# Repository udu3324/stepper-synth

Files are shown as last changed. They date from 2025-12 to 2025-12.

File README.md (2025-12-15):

# stepper-synth

An electronic instrument that uses stepper motors to make music. Powered by the esp32 ecosystem, it is a synthesizer with 3 octaves with velocity support using hall effect sensors. It is inspired by the musician/engineer [Love Hultén](https://www.youtube.com/@hulten1000).

## Why I Made This

There's so many electronic instruments that make sounds purely through cables and rely on other devices to output to them. Instead, what if I used the power of stepper motors to make sound and create a standalone device? I notice how harmonic these motors could be while 3d printing, they sometimes have a noticable pattern and variable pitch that can be utilized.

## Photos

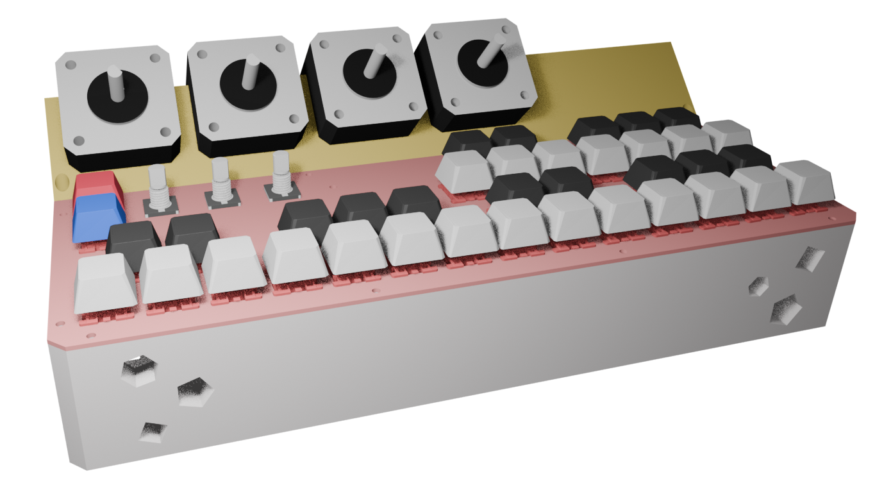
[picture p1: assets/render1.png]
render

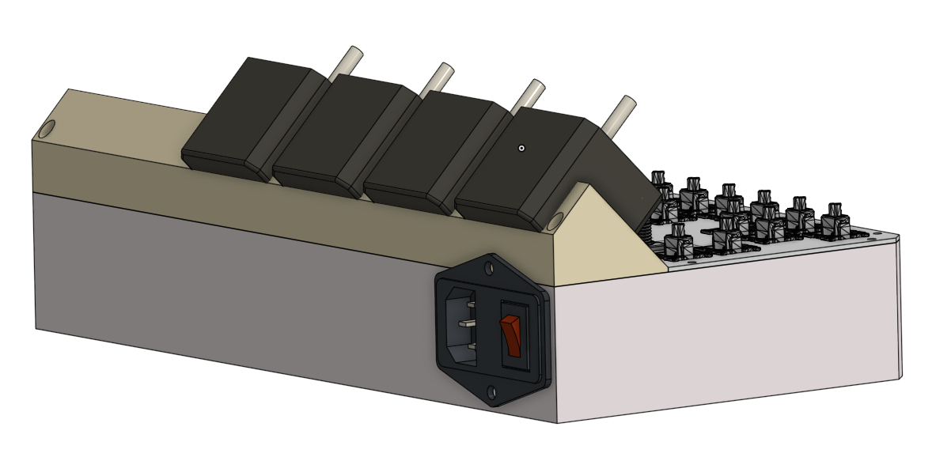
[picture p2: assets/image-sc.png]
sc1

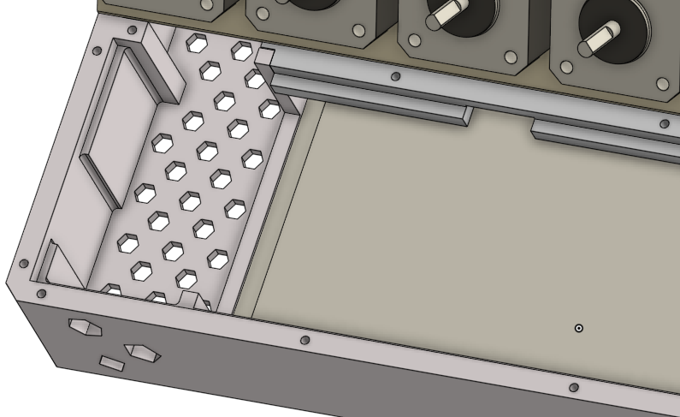
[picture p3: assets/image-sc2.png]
sc2


## PCB

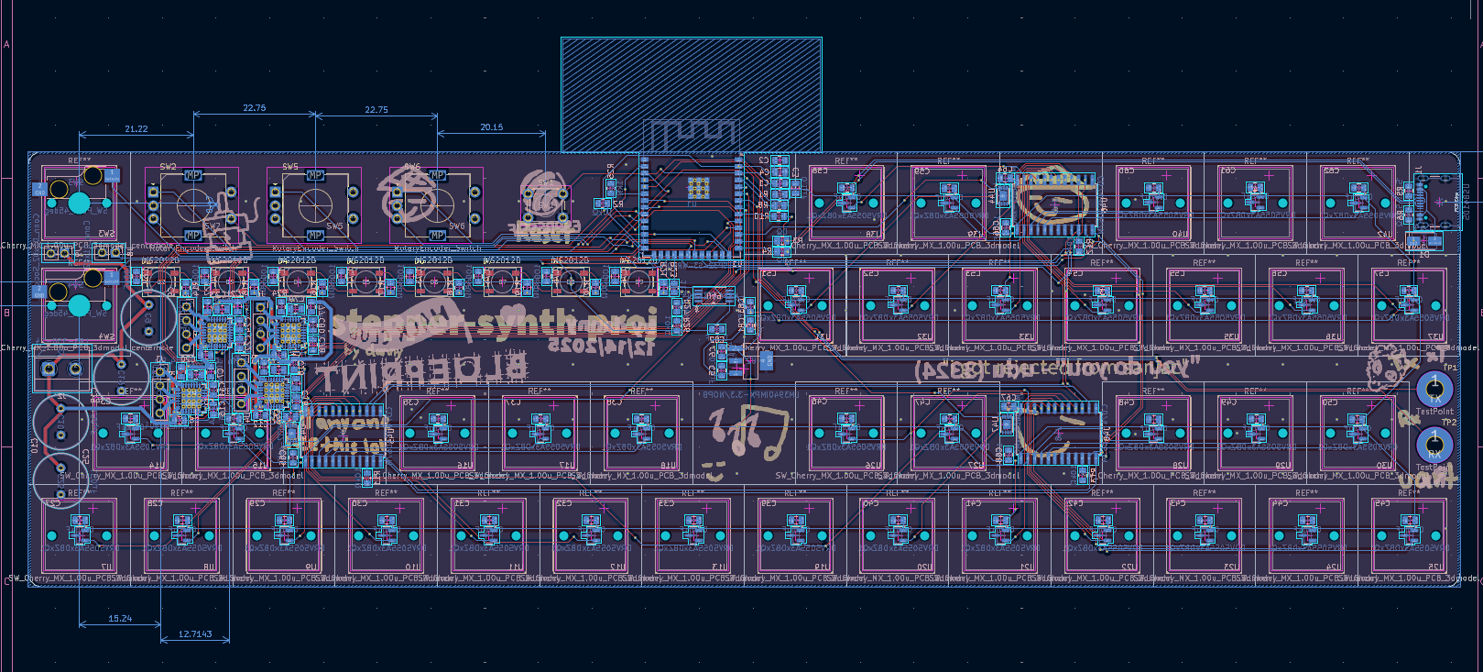
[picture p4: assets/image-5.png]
pcb

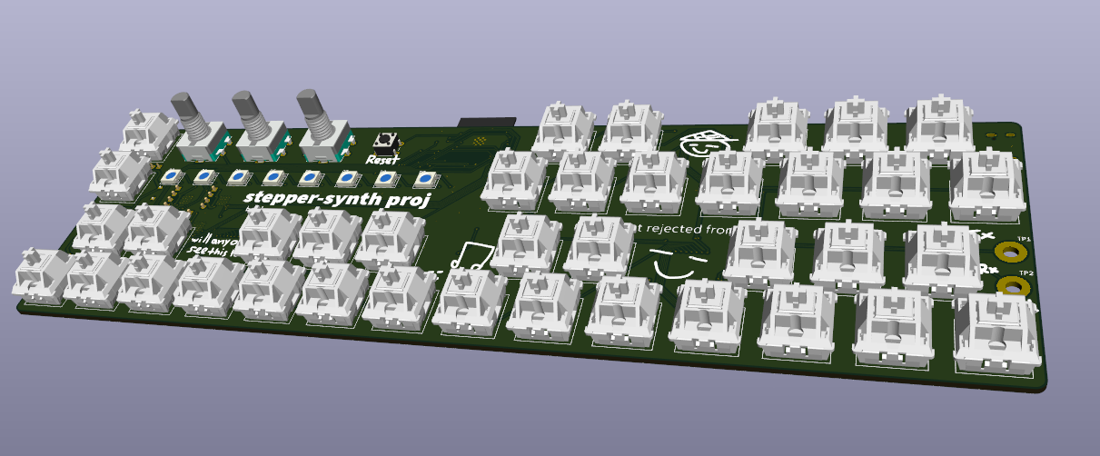
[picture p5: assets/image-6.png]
3d pcb


## Schematics

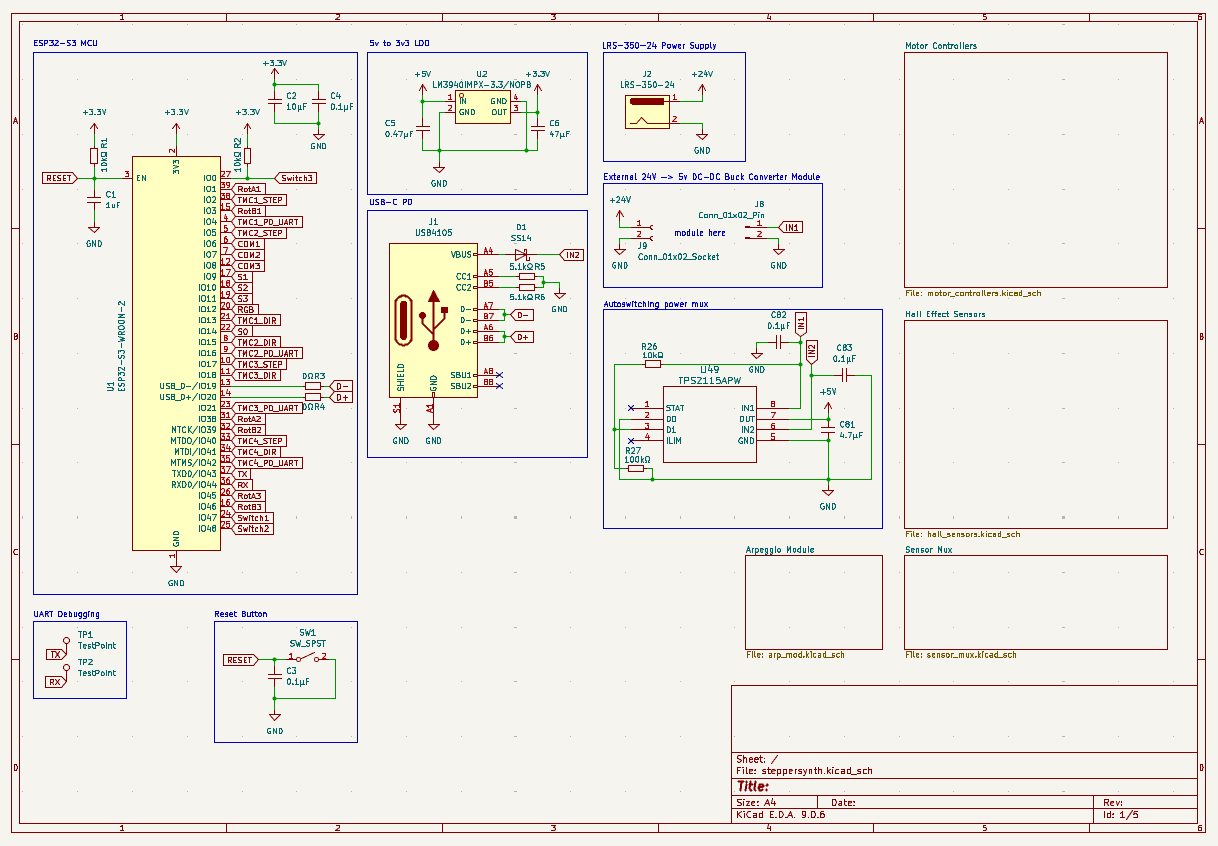
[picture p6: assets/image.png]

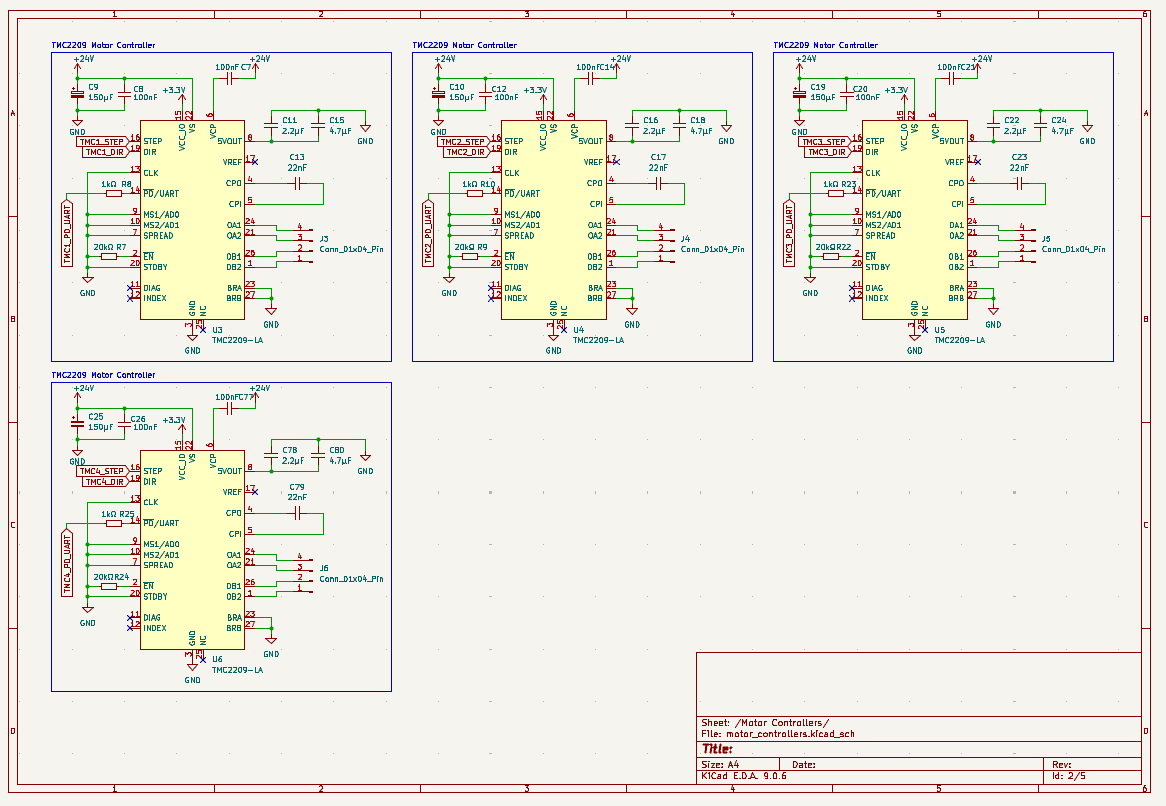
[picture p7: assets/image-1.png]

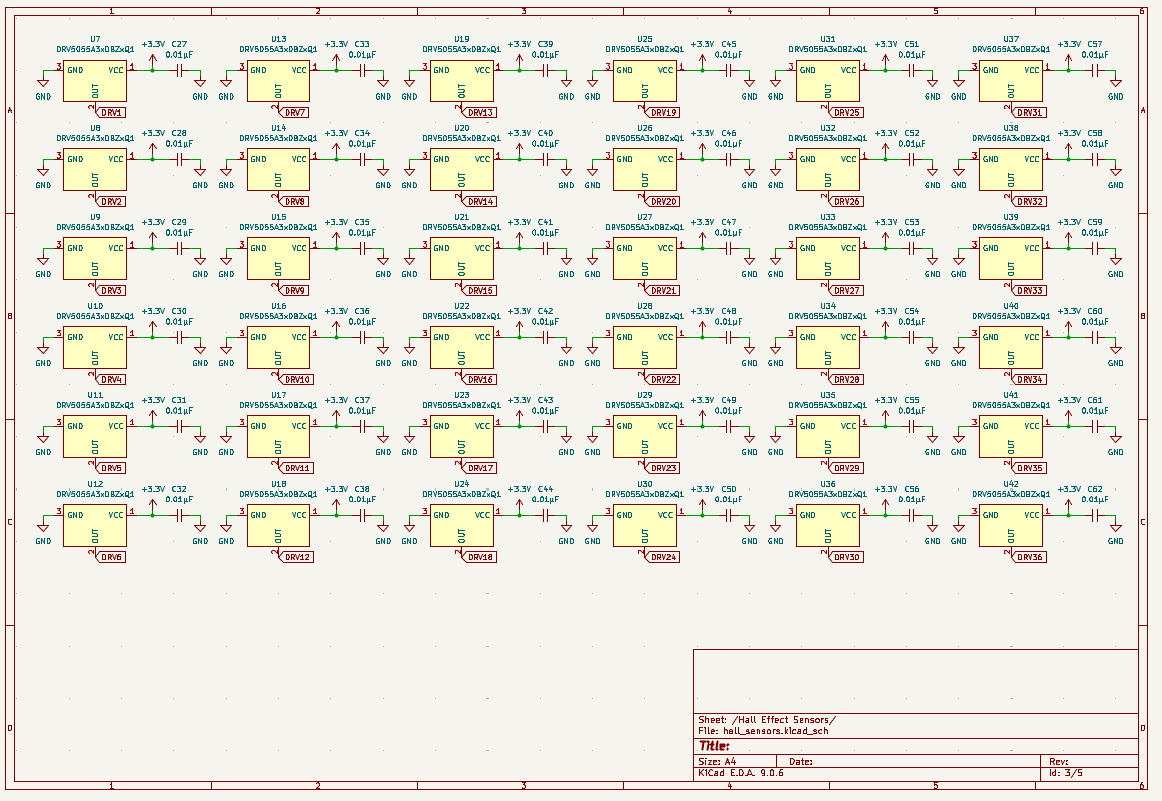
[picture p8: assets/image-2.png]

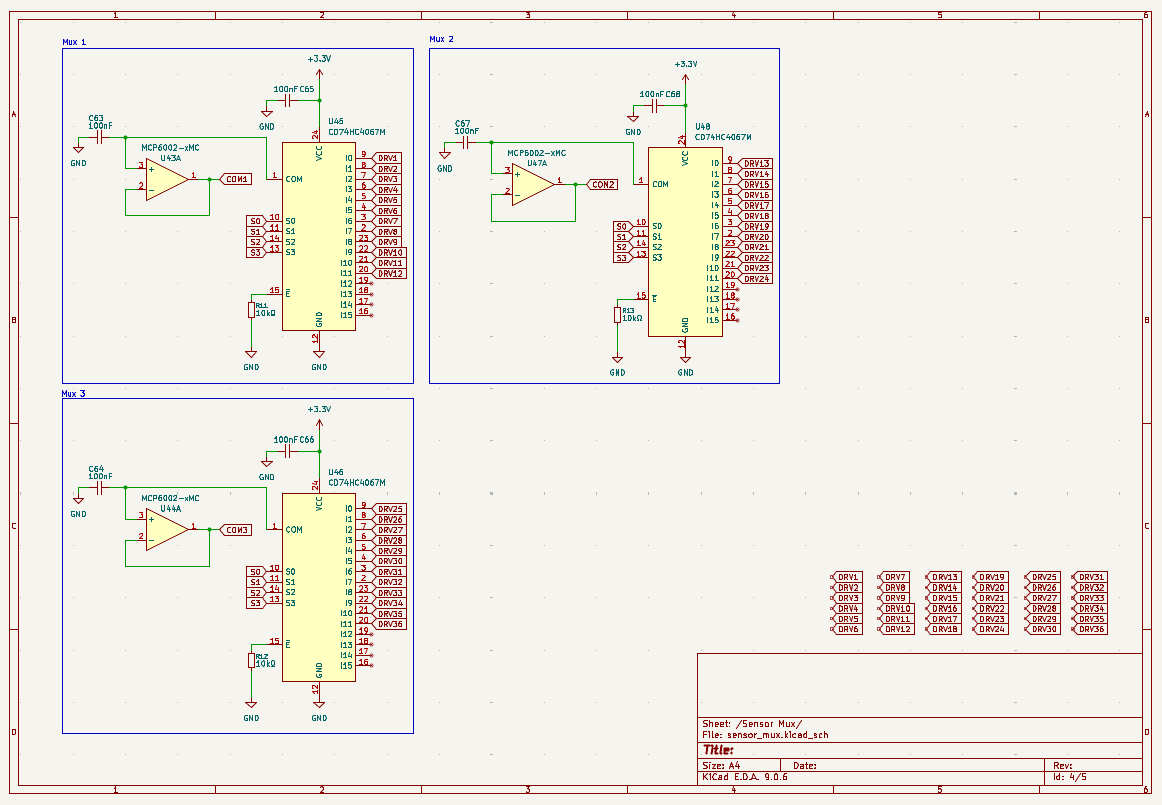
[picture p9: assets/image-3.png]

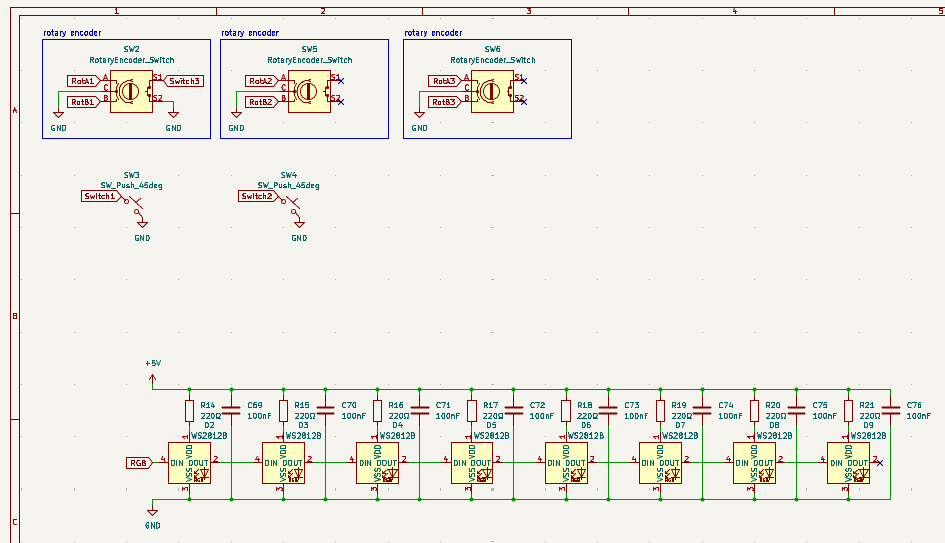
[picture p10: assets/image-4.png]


## Bill of Materials

Sadly I was aiming for tier 2 budget but didn't realize how much tariffs and shipping would push me out of it 😭

Interactive Link: [google sheets](https://docs.google.com/spreadsheets/d/12KobohwvsCrDZkVZn1qAy473UDQfyoO-3Iqs66wPygc/edit?usp=sharing)

|Part |Cost |Count|Count Cost|Note |Status |Link |
|---|---|-----|---|---|---|---|
|Regular Switches | |2 |0 | |On hand|https://divinikey.com/collections/linear-switches |
|Hall Effect Switches |$13.50 |2 |$27.00 |18x per | |https://divinikey.com/collections/hall-effect-switches/products/gateron-magnetic-genty-he-switches |
|Rotary Encoder | |3 |0 | |On hand|https://www.mouser.com/ProductDetail/Alps-Alpine/EC11E183440C?qs=YMSFtX0bdJC6PoDF7K4k%252Bg%3D%3D |
|Button | |1 |0 | |On hand|https://www.digikey.com/en/products/detail/te-connectivity-alcoswitch-switches/1825910-6/1632536 |
|WS2812 |$0.80  |8 |$6.40 |neopixels | |https://www.mouser.com/ProductDetail/SparkFun/COM-24837?qs=dbcCsuKDzFUNFvBH5VYBTw%3D%3D |
|LRS-350-24 | |1 |0 |power supply |On hand|https://www.digikey.com/en/products/detail/mean-well-usa-inc/LRS-350-24/7705034 |
|IEC320 C14 Switch | |1 |0 |cable input |On hand|https://www.aliexpress.us/item/3256804155743663.html |
|Screw Terminal |$0.35  |1 |$0.35 | | |https://www.mouser.com/ProductDetail/Same-Sky/TB002-500-02BE?qs=vLWxofP3U2x9716kcgva%2Fw%3D%3D |
|Nema 17 0.8 Motors | |4 |$0.00 |reused prusas |On hand|https://www.omc-stepperonline.com/nema-17-bipolar-0-9deg-46ncm-65-1oz-in-2a-2-9v-42x42x48mm-4-wires-17hm19-2004s |
|ESP32-S3-WROOM-2 |$11.87 |1 |$11.87 |microcontroller | |https://www.mouser.com/ProductDetail/Espressif-Systems/ESP32-S3-WROOM-2-N32R16V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 |
|Solder Paste Syringe |$16.95 |1 |$16.95 |mine dried out | |https://www.mouser.com/ProductDetail/Chip-Quik/TS391LT?qs=1mbolxNpo8dzjCIcP7S2Kg%3D%3D |
|150uF Polarized Capacitor|$1.40  |4 |$5.60 | | |https://www.mouser.com/ProductDetail/Panasonic/EEH-AZA1E151B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 |
|Female Pin Headers |$0.84  |2 |$1.68 | | |https://www.mouser.com/ProductDetail/Samtec/CES-102-02-G-S?qs=0lQeLiL1qyY%2FrwXtinpohw%3D%3D |
|Hot-swap Switch Plug | |2 |0 | |On hand|https://www.gateron.com/products/gateron-low-profile-switch-hot-swap-pcb-socket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|
|M3x5mm Screws | |18 | | |On hand|https://www.moddiy.com/products/1264/M3.0-x-5mm-Black-Screws-(KM3X5).html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 |
| | | | | | | |
|PCB Prototype |$12.20 | | | | | |
|PCBA |$90.68 | | |6 extended parts only | | |
|Merchandise Total |$102.88| | |pcb + pcba | | |
|Shipping Estimate |$55.24 | | | | | |
|Duties & Taxes (US) |$46.30 | | | | | |
|Sales Tax |$13.04 | | | | | |
|Grand Total |$217.46| | |only count this | | |
| | | | | | | |
| |$217.46| |69.85 | | | |
| | | | | | | |
|Needed for Grant |$287.31| | |not including shipping and taxes from mouser/divinikey!!!| | |
| | | | |though mouser shipping should be really low | | |

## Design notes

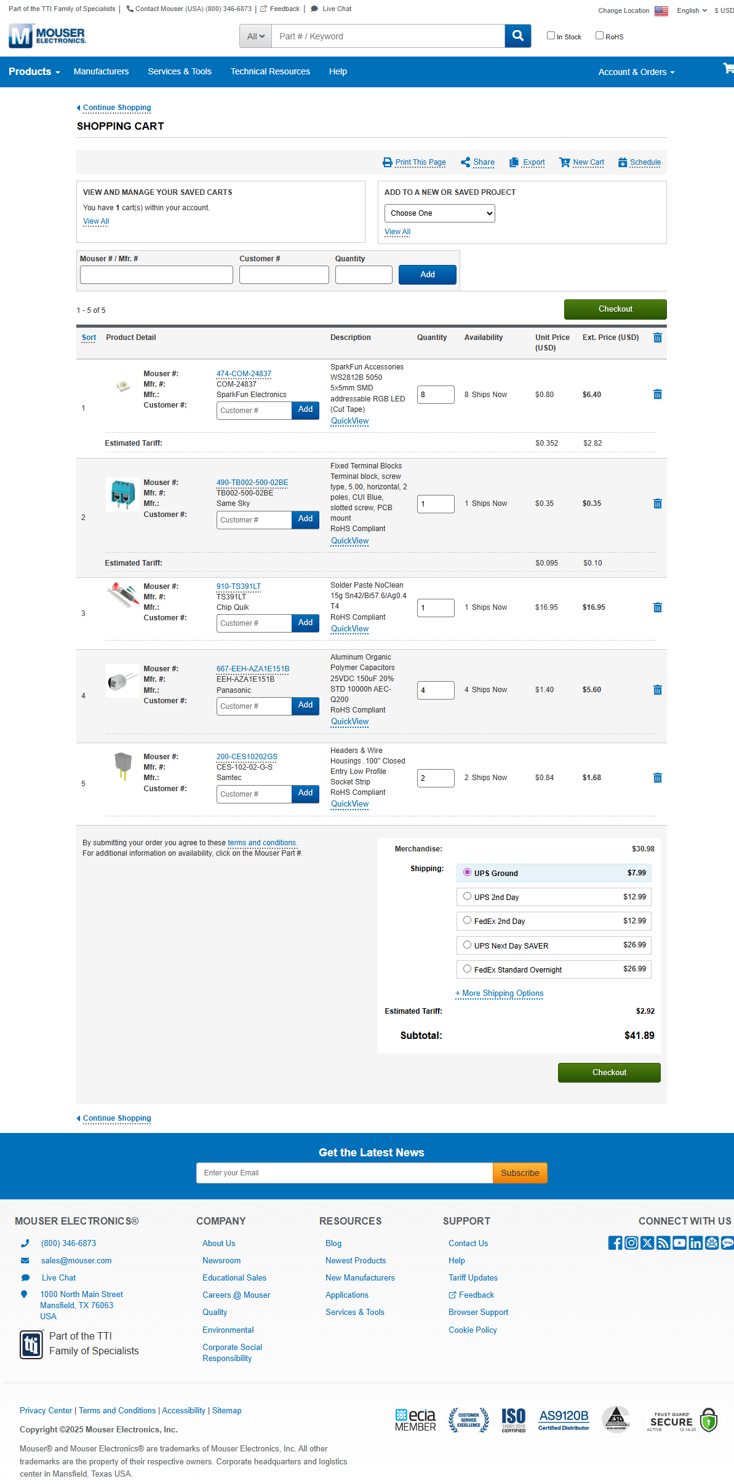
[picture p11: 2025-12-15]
mouser cart NEW.png

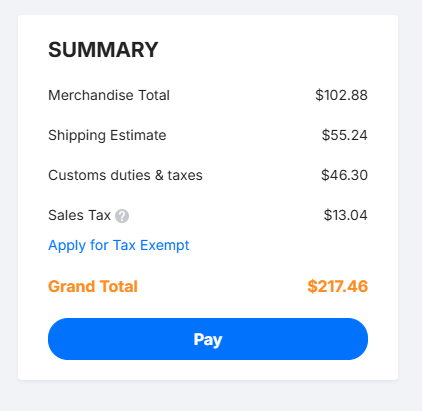
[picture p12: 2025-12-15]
jlcpcb grand total.png

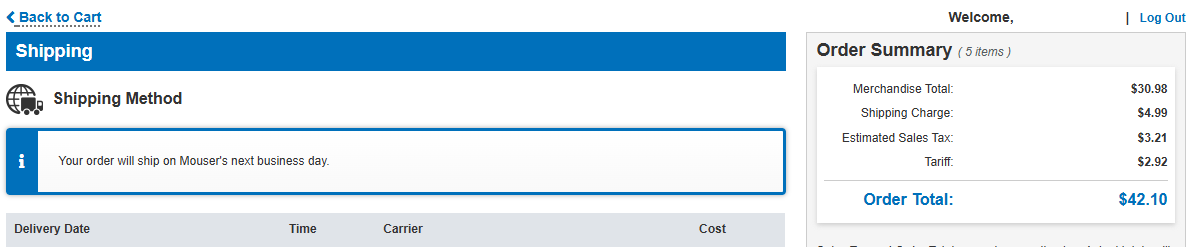
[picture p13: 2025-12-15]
mouser grand total NEW.png

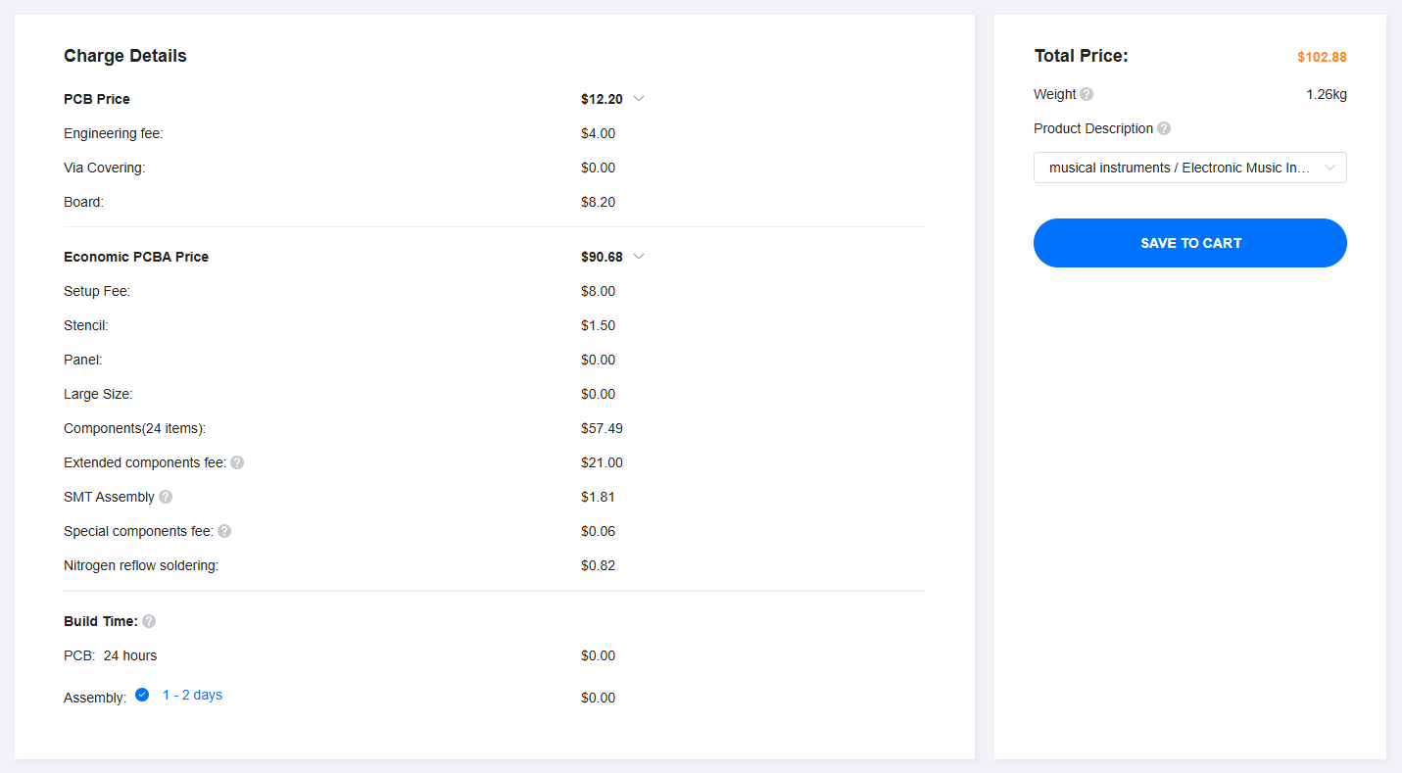
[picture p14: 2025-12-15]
jlcpcb pcba breakdown.png

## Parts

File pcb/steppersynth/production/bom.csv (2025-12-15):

Designator | Footprint | Quantity | Value | LCSC Part #
C1 | 0805 | 1 | 1uF
C10, C19, C25, C9 | C_Radial_D10.0mm_H12.5mm_P5.00mm | 4 | 150µF
C11, C16, C22, C78 | 0805 | 4 | 2.2µF
C12, C14, C20, C21, C26, C63, C64, C65, C66, C67, C68, C69, C7, C70, C71, C72, C73, C74, C75, C76, C77, C8 | 0805 | 22 | 100nF
C13, C17, C23, C79 | 0805 | 4 | 22nF
C15, C18, C24, C80, C81 | 0805 | 5 | 4.7µF
C2 | 0805 | 1 | 10μF
C27, C28, C29, C30, C31, C32, C33, C34, C35, C36, C37, C38, C39, C40, C41, C42, C43, C44, C45, C46, C47, C48, C49, C50, C51, C52, C53, C54, C55, C56, C57, C58, C59, C60, C61, C62 | 0805 | 36 | 0.01µF
C3, C4, C82, C83 | 0805 | 4 | 0.1μF
C5 | 0805 | 1 | 0.47μF
C6 | 0805 | 1 | 47μF
D1 | D_SMA | 1 | SS14
D2, D3, D4, D5, D6, D7, D8, D9 | LED_WS2812B_PLCC4_5.0x5.0mm_P3.2mm | 8 | WS2812B
J1 | USB_C_Receptacle_GCT_USB4105-xx-A_16P_TopMnt_Horizontal | 1 | USB4105
J2 | TerminalBlock_MetzConnect_Type055_RT01502HDWU_1x02_P5.00mm_Horizontal | 1 | LRS-350-24
J3, J4, J5, J6 | PinHeader_1x04_P2.54mm_Vertical | 4 | Conn_01x04_Pin
J8 | PinSocket_1x02_P2.54mm_Vertical | 1 | Conn_01x02_Pin
J9 | PinSocket_1x02_P2.54mm_Vertical | 1 | Conn_01x02_Socket
R1, R11, R12, R13, R2, R26 | 0805 | 6 | 10kΩ
R10, R23, R25, R8 | 0805 | 4 | 1kΩ
R14, R15, R16, R17, R18, R19, R20, R21 | 0805 | 8 | 220Ω
R22, R24, R7, R9 | 0805 | 4 | 20kΩ
R27 | 0805 | 1 | 100kΩ
R3, R4 | 0805 | 2 | 0Ω
R5, R6 | 0805 | 2 | 5.1kΩ
SW1 | SW_PUSH_6mm | 1 | SW_SPST
SW2, SW5, SW6 | RotaryEncoder_Alps_EC11E-Switch_Vertical_H20mm | 3 | RotaryEncoder_Switch
SW3, SW4 | TH_L10.9-W5.9-CPG151101S11 | 2 | SW_Push_45deg
TP1, TP2 | MountingHole_3.2mm_M3_Pad | 2 | TestPoint
U1 | ESP32-S3-WROOM-2 | 1 | ESP32-S3-WROOM-2
U10, U11, U12, U13, U14, U15, U16, U17, U18, U19, U20, U21, U22, U23, U24, U25, U26, U27, U28, U29, U30, U31, U32, U33, U34, U35, U36, U37, U38, U39, U40, U41, U42, U7, U8, U9 | SOT-23 | 36 | DRV5055A3xDBZxQ1
U2 | SOT-223-4_L6.5-W3.5-P2.30-LS7.0-BR | 1 | LM3940IMPX-3.3/NOPB | C544820
U3, U4, U5, U6 | VQFN-28-1EP_5x5mm_P0.5mm_EP3.7x3.7mm_ThermalVias | 4 | TMC2209-LA
U43, U44, U47 | DFN-8-1EP_3x2mm_P0.5mm_EP1.75x1.45mm | 3 | MCP6002-xMC
U45, U46, U48 | SOIC-24W_7.5x15.4mm_P1.27mm | 3 | CD74HC4067M
U49 | PW8 | 1 | TPS2115APW

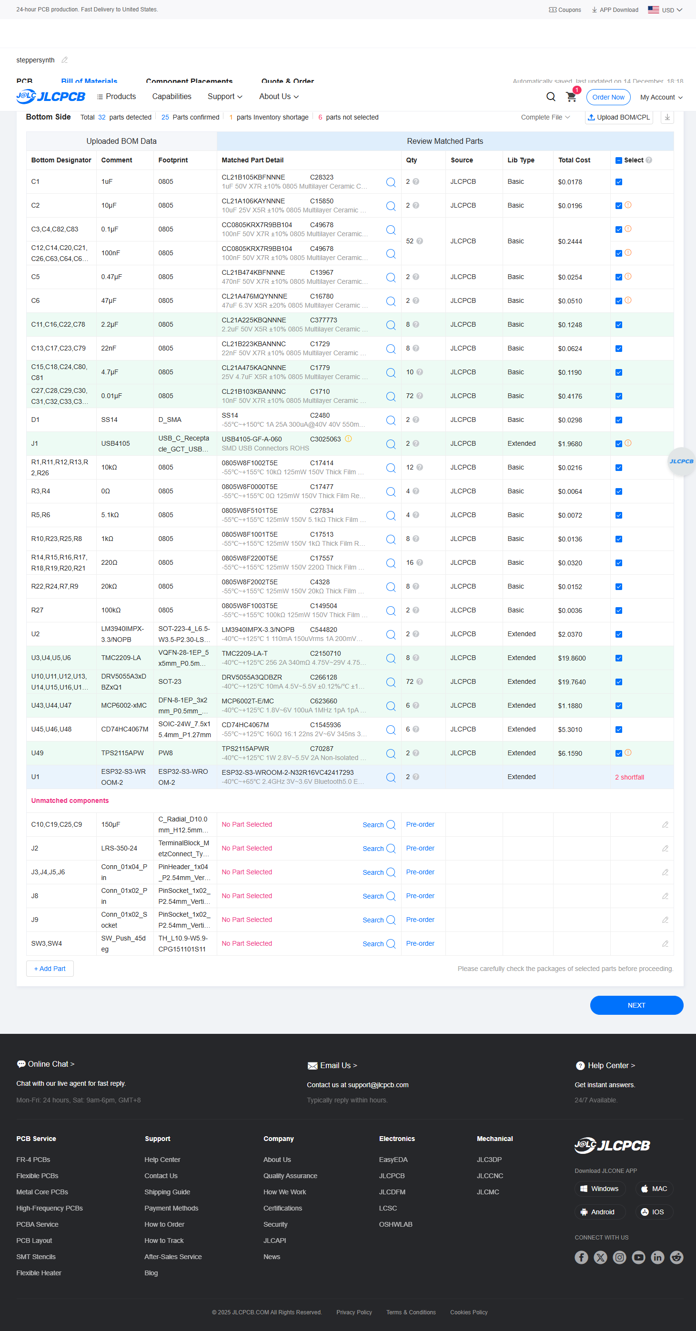
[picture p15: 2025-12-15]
jlcpcb pcba components breakdown 2.png

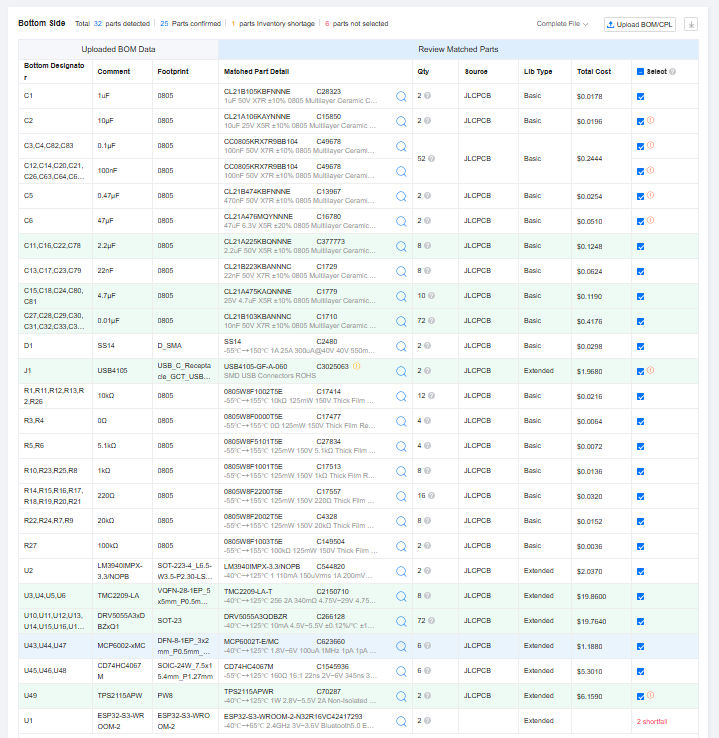
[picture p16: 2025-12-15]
jlcpcb pcba components breakdown.png

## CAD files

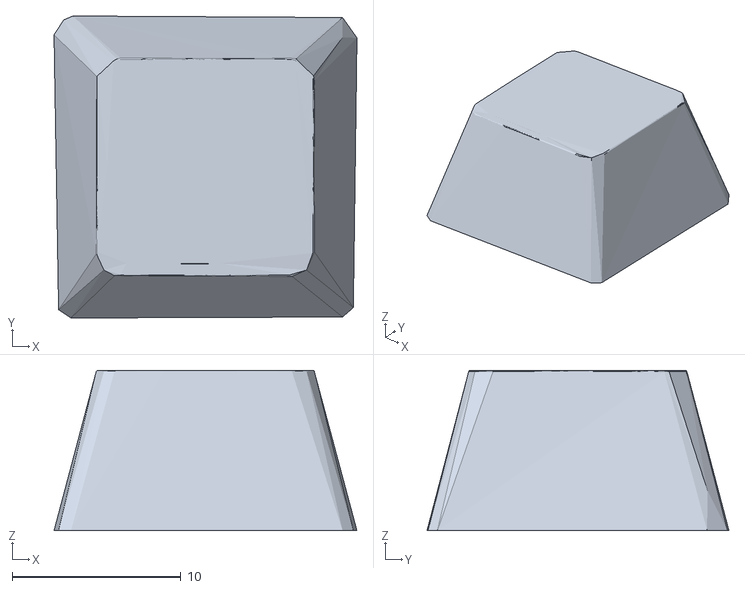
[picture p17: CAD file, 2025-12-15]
assets/Simple-CherryMX-Keycap.stl
18.0 x 17.9 x 9.50

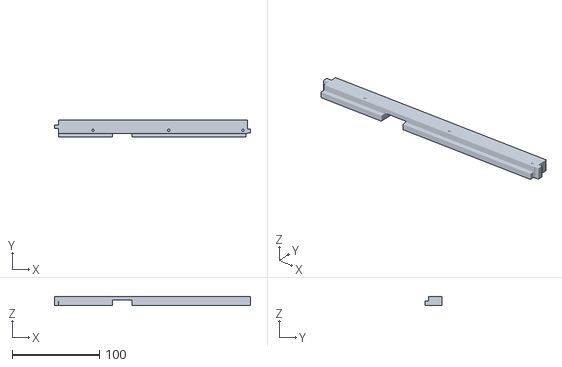
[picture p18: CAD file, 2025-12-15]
cad/case - plate mount support.stl
224.6 x 19.0 x 10.1

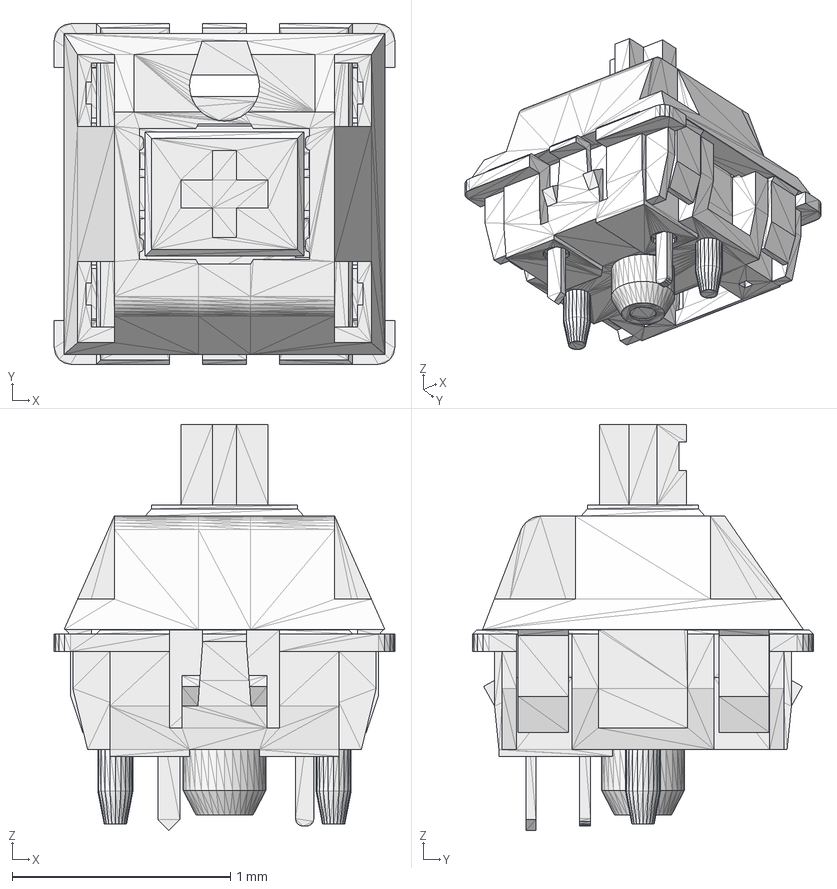
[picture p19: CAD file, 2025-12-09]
pcb/cherry mx switch.step
1.56 x 1.56 x 1.86 mm

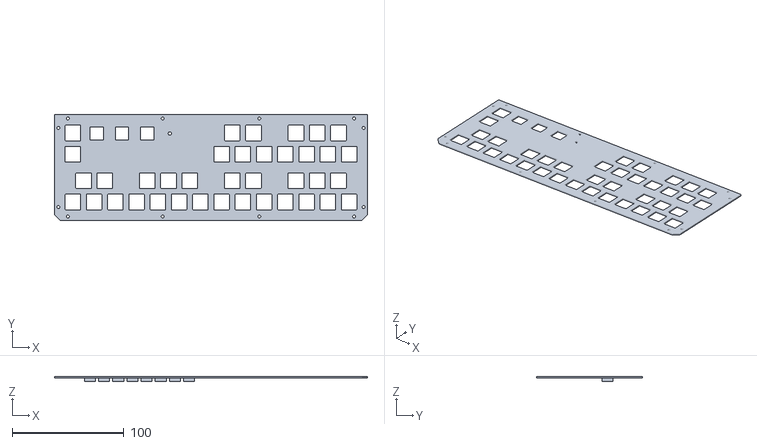
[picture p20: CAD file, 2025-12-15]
cad/case - Plate.stl
280.7 x 95.0 x 4.75

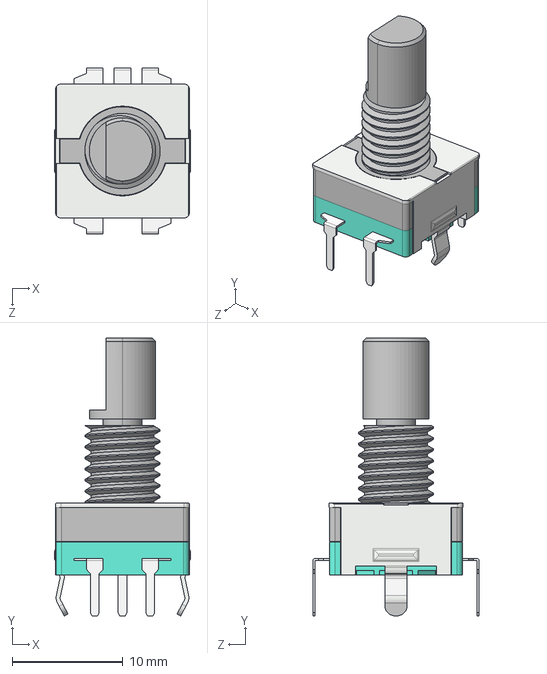
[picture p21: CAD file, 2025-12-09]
pcb/ec11 rotary encoder.STEP
12.3 x 25.1 x 15.0 mm

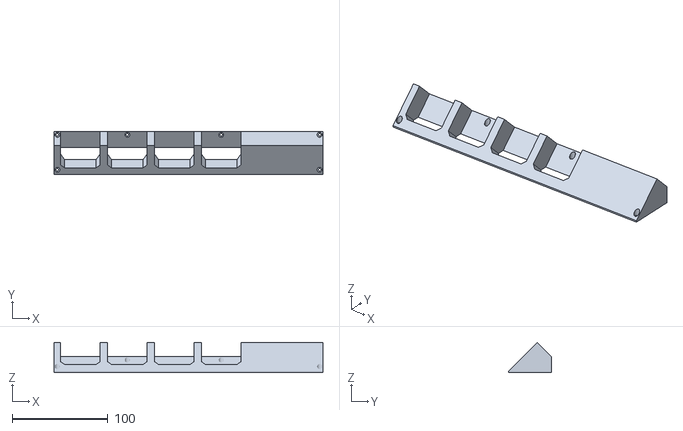
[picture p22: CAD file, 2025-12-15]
cad/case - motor mount.stl
280.7 x 45.0 x 31.7

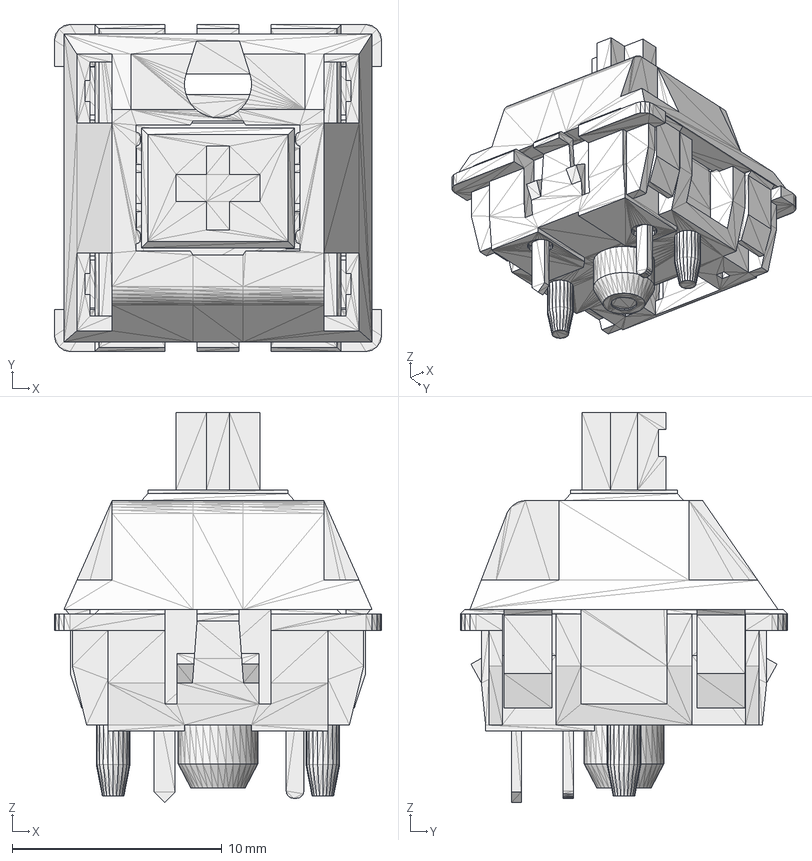
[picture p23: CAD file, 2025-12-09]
pcb/cherry mx switch resized 2.step
15.6 x 15.6 x 18.6 mm

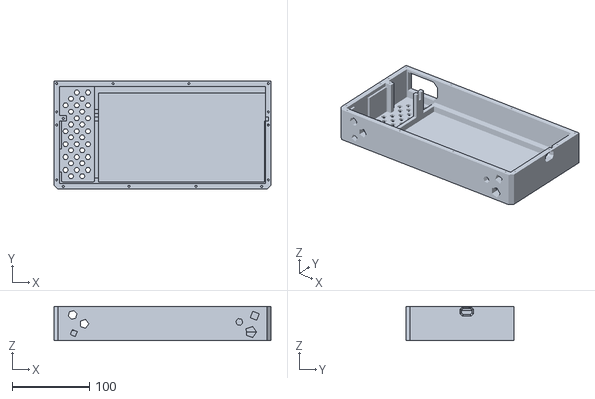
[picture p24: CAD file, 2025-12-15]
cad/case - case.stl
280.7 x 140.0 x 44.0

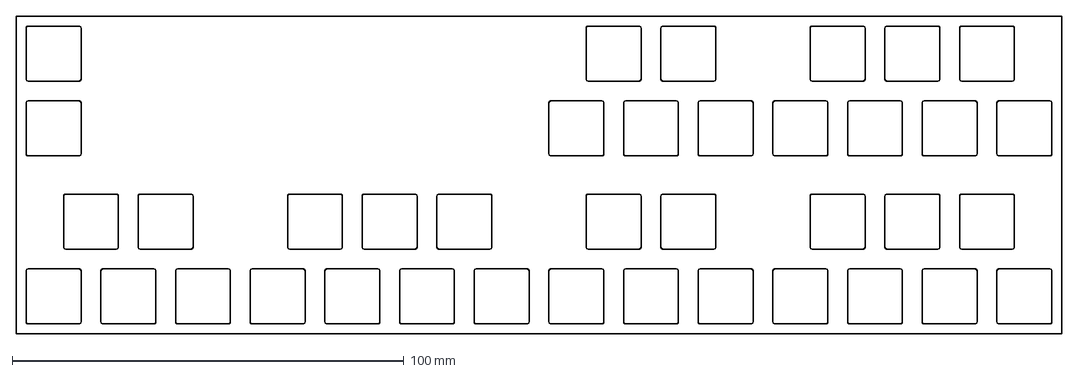
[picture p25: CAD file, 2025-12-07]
cad/plate-2025-12-06T02_20_04.977Z.dxf
266.7 x 81.0 mm

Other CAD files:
pcb/cherry mx switch resized 2.stl
pcb/cherry mx switch.stl

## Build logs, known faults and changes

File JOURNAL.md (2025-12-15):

Total time before submission: 61.5 hours

# December 1 - Planning Idea
**Total time spent: 5.5 hours**

Today i started drafting my idea on paper and researched what components i would use.

Features
- Possibly midi in?
- Maybe built in mic?
- Velocity support for keys
- Arpeggio module for effects
- 2-3 octave keyboard
- Portable, similar dimensions to a 75% keyboard

Components
- External psu for 4 stepper motors
- CD74HC4067 Analog mux i found from ti with 16:1 channels
- TMC2209 motor controller 
- DRV5053 analog hall sensors for hall effect key switches
- Esp32-s3 module

A major problem was finding a way to connect all 36 hall effect sensors to an esp32. Multiplexing isnt really my strong suit and i have some ptsd from doing it from a previous project.

b

# December 3 - Starting the Schematics
**Total time spent: 6 hours**

## MCU Setup

The microcontroller setup was pretty straightforward. 5v power was from usb-c and going through a LDO for 3v3 power for logic for the esp32.



## TMC2209 Implementation

This was super hard as I had to design my own implementation of the IC for my specific use case. I had to reference many different resources including already made modules and the datasheet.

**References**
- [official datasheet](https://www.analog.com/media/en/technical-documentation/data-sheets/TMC2209_datasheet_rev1.09.pdf)
- [adafruit tmc2209 breakout board eagle files](https://github.com/adafruit/Adafruit-TMC2209-Breakout-PCB)
- [random schematic png](https://microcontrollerslab.com/wp-content/uploads/2021/03/TMC2209-Stepper-Motor-Driver-module-internal-circuit-diagram-768x377.jpg)
- [random schematic png 2](https://image.easyeda.com/components/e375a9ddb5db4d86a2d0d3d4b046859c.png)



I'm not entirely sure if my implementation is right or great... What got me really confused was how this IC could function without a MCU with all of its configuration pinouts, but I could really just do this all with the UART.

# December 4 - Creating Schematic for Multiplexer and Sensors
**Total time spent: 5 hours**

I think my implementation is alright. The sheer amount of sensors I am using definitely requires me to use a multiplexer as there isn't enough GPIO on the esp32-s3.

At first, I thought it would be really complicated to use the mux ic, but it was really simple and just acts like a switch between all the connected IO. The S0,1,2,3 accept binary to switch between all the connected devices and sends them to COM. I was told that my use case with tons of analog devices required an op-amp for stable voltage when switching.

I also used a bunch of resources below!

- [mux datasheet](https://www.ti.com/lit/ds/symlink/cd74hc4067.pdf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)
- [op-amp datasheet](https://ww1.microchip.com/downloads/aemDocuments/documents/MSLD/ProductDocuments/DataSheets/MCP6001-1R-1U-2-4-1-MHz-Low-Power-Op-Amp-DS20001733L.pdf)
- [forum post on the mux](https://forum.arduino.cc/t/cd74hc4067-arduino/1116756)
- [sparkfun's mux breakout board schematic](https://cdn.sparkfun.com/datasheets/BreakoutBoards/Analog-Digital-Mux-Breakout-v11.pdf)

In the end, i think it'll function pretty solid



# December 6 - Finishing up schematic, defining footprints for symbols
**Total time spent: 7 hours**

## Connecting Components to MCU

I decided to skip connecting all my components to my mcu until the end as i knew it would be time consuming to check which pins were capable of what... and i was right.

A bunch of checking if GPIO or ADC was supported for specific pins. There were so many limitations that I sadly had to remove one rotary encoder in my design as well as two buttons that are linked to two encoders. 

I double, even triple checked if the io i used was safe and there was so much conflicting info due to there being multiple revisions of the esp32-s3. In the end, IO6-12 are actually safe to use and kicad's symbol is correct as the SPI flash io is between IO21-30 which is why they're omitted. I THINK.



Anyways, In the end i was able to use up all of my GPIO lol.



IO47 + 48 are also not on 3.3v logic high for some reason...

## Footprints

I decided to use mostly all 0805 size components for resistors and capacitors as they should be common and standard component for PCBA. For my external PSU, i am using a 5mm pitch screw terminal. I also will use a hot-swappable key switch thing for my two octave change keys





# December 7 - Component Positioning
**Total time spent: 7 hours**

I positioned everything on my board. It took quite a while as I had to search back through some datasheets as they recommend a distance between some components, like pulldowns and capacitors for the hall effect sensors.

I generated a outline file for my keyboard switches and based the board size off of it. This would let me know every position of the keys n stuff.

One thing that I had to also account for was the space underneath the pcb. The power supply i was using was pretty large, and it limited places of where I could put components that stuck out (screw terminals, heatsinks for tmc2209 drivers, pinheaders, etc)



# December 8 - DC-DC Buck Converter + Auto Power Switch
**Total time spent: 3 hours**

Since my design has two power sources, one from a power supply and another from USB power delivery, i would have to manage which power I am going to use.

Ideally I should support all these conditions below

- USB plugged in, PSU not plugged in (esp32/logic is powered, motors cant drive, ideal for developing firmware)
- USB unplugged, PSU plugged in (both esp32 and stepper motor ics are powered and can drive, for production)
- Both USB and PSU plugged in (same as above but can also push code and run motors at the same time)

First, I need to turn 24v to 5v. I can do this with a simple DC-DC Buck Converter module i found.

Now, I can then use a TPS2115A to switch between two 5v sources and then output to the LDO instead of USB PD doing it directly.

I used a bunch of sources including the ones below to help wire the IC!

- [ti forum post 1](https://e2e.ti.com/support/power-management-group/power-management/f/power-management-forum/962334/tps2115-backdriving)
- [ti forum post 2](https://e2e.ti.com/support/power-management-group/power-management/f/power-management-forum/969018/tps2115a-using-in1-as-input-for-d1)
- [official datasheet](https://www.ti.com/product/TPS2115A)



# December 10 - Cadded a Bunch of Stuff
**Total time spent: 18 hours**

This entry is a combination of work spread around 4ish days or more. I chose to do this on onshape as i am very annoyed at how slow fusion 360 loads. 

## Measuring Parts On Hand

I needed to measure parts i had on hand and model some references. This included my ac plug, stepper motors, and power supply.



## Importing and Designing around the PCB Model

Kicad has this feature where i can export a 3d model (step file) and import into onshape to take solid dimensions of. At first i had issues with lag but i remembered that all the caps/resistors were also included and fixed that.



With this, I started designing the plate that fits the keycaps, neopixels (shining through a thin layer of plastic), and rotary encoders. I could then build a case around it fastened with M3 screws i have laying around.

chrome_lmEsddRs0H



The PCB would be held in through the keycaps in the plate, but is also supported by a inner lip inside the case

A press fit mount was made for the power supply as well



The power supply is also held with this bar that hugs the power supply and stops the plate from sagging



Lastly, a motor mount was made to stylishly display the stepper motors at a 45 degree angle to the user. It is also press fit lol



## End result

Overall, i think its a really solid cad design but kinda bland, I'll probably add some holes to allow the user to see inside of it later.

chrome_8n2NrPDpo4



# December 13 - Routed PCB
**Total time spent: 6 hours**

I started routing my PCB but saw a few mistakes on my schematic while doing so. The pinout for TMC2209 to my specific stepper motor was a little different with the coil pairs being together instead of separated. Some previous placement of footprints also didnt make sense and i definitely could of chose specific pins based on their physical location. (analog muxes) 

I tried ignoring this problem until now, but I've never routed any power lines above 5v before. Looking at TMC2209 modules sold online, they of course have thick traces coming from OA1/OA2/OB1/OB2. I wasn't sure how thick mine were going to be, but definitely not the 0.3mm default. 

I first did 1.0mm thickness which took tons of space, but after some chatting and doing some research, 0.6mm seemed like it would work.



My workflow was something like this:

- Route the hall effect sensors and mux first
- Give power traces priority, and also traces farthest from the esp32 pin
- Also give analog traces more priority over digital ones
- Try not to use too many vias to jump across traces
- its literally a game of chess, but kicad (iykyk)

Overall, my routing was good enough

For final touches, I tried something new called via stitching



# December 14 - Final Touches
**Total time spent: 4 hours**

I pretty have everything done! But i need to fix some small issues and also have some flare

## Cad

The cad was improved a little. I added some cool extruded geometry on the side seen by users, and filleted corners in the x/y axis for 3d print optimization.





## PCB

I made sure to use as many basic parts as i could and only am doing PCBA on one side. I will have to solder on some components, including the MCU, neopixels, bulk caps, and more. 

I also created some cool silkscreens for the front and back of my pcb since there was empty space



## BOM

I started writing my bom



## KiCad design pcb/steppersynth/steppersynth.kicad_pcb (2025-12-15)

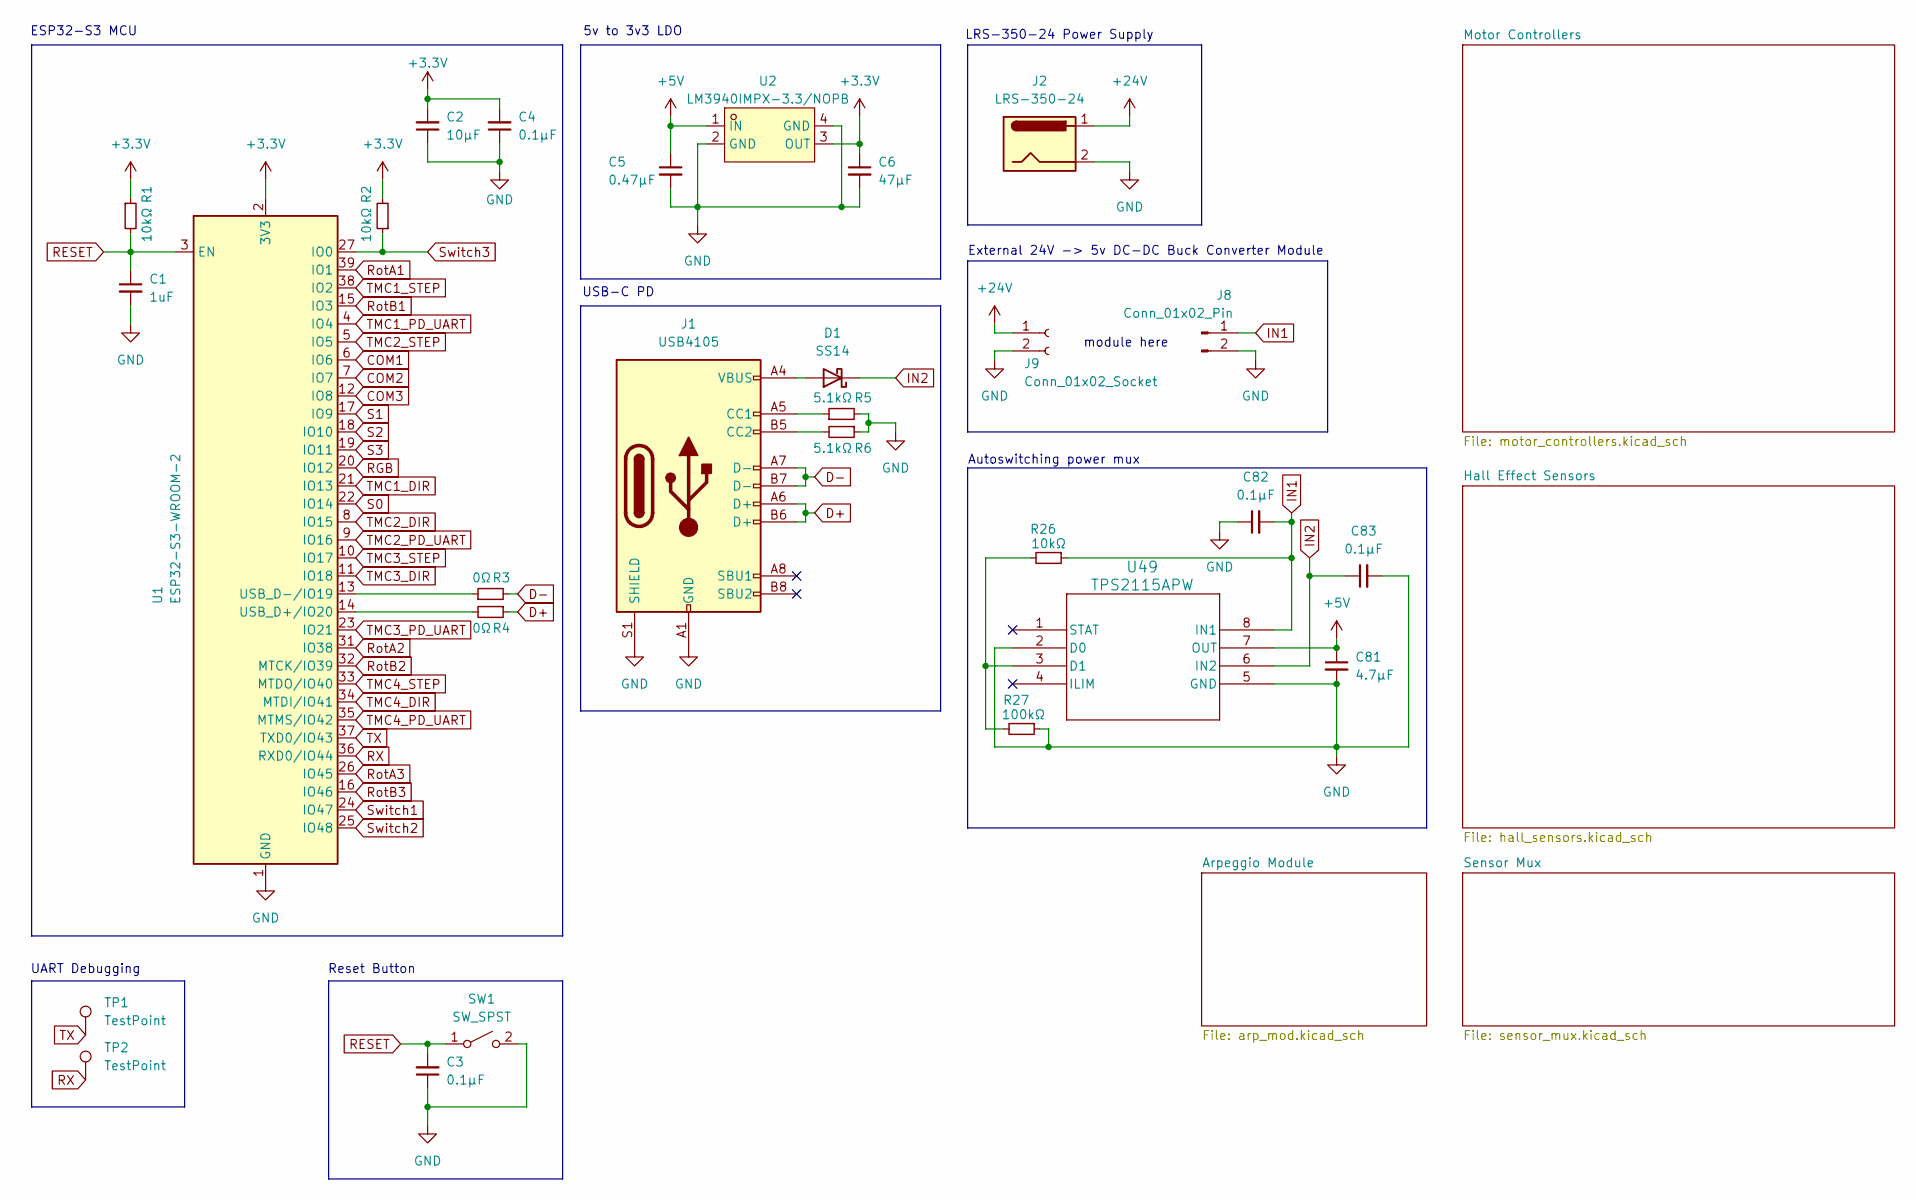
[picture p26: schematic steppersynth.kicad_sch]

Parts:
C1: 1uF; C_0805_2012Metric
C2: 10μF; C_0805_2012Metric
C3, C4, C82, C83: 0.1μF; C_0805_2012Metric
C5: 0.47μF; C_0805_2012Metric
C6: 47μF; C_0805_2012Metric
C81: 4.7μF; C_0805_2012Metric
D1: SS14; D_SMA
J1: USB4105; USB_C_Receptacle_GCT_USB4105-xx-A_16P_TopMnt_Horizontal
J2: LRS-350-24; TerminalBlock_MetzConnect_Type055_RT01502HDWU_1x02_P5.00mm_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
J8: Conn_01x02_Pin; PinSocket_1x02_P2.54mm_Vertical
J9: Conn_01x02_Socket; PinSocket_1x02_P2.54mm_Vertical
R1, R2, R26: 10kΩ; R_0805_2012Metric
R3, R4: 0Ω; R_0805_2012Metric
R5, R6: 5.1kΩ; R_0805_2012Metric
R27: 100kΩ; R_0805_2012Metric
SW1: SW_SPST; SW_PUSH_6mm
TP1, TP2: TestPoint; MountingHole_3.2mm_M3_Pad
U1: ESP32-S3-WROOM-2
U2: LM3940IMPX-3.3/NOPB; SOT-223-4_L6.5-W3.5-P2.30-LS7.0-BR; LCSC Part C544820
U49: TPS2115APW; PW8

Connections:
+3.3V: C2.2, C4.2, C6.1, R1.1, R2.2, U1.2 (3V3), U2.3 (OUT); also elsewhere on the board
+5V: C5.1, C81.1, U2.1 (IN), U49.7 (OUT); also elsewhere on the board
+24V: J2.1, J9.1; also elsewhere on the board
COM1: U1.6 (IO6); also elsewhere on the board
COM2: U1.7 (IO7); also elsewhere on the board
COM3: U1.12 (IO8); also elsewhere on the board
D+: J1.A6 (D+), J1.B6 (D+), R4.1
D-: J1.A7 (D-), J1.B7 (D-), R3.2
GND: C1.2, C2.1, C3.1, C4.1, C5.2, C6.2, C81.2, C82.1, C83.2, J1.A1 (GND), J1.A12 (GND), J1.B1 (GND), J1.B12 (GND), J1.S1 (SHIELD), J2.2, J8.2, J9.2, R5.2, R6.1, R27.1, SW1.2 (B), U1.1 (GND), U1.40 (GND), U1.41 (GND), U2.2 (GND), U2.4 (GND), U49.2 (D0), U49.5 (GND); also elsewhere on the board
IN1: C82.2, J8.1, R26.1, U49.8 (IN1)
IN2: C83.1, D1.1 (K), U49.6 (IN2)
unnamed: D1.2 (A), J1.A4 (VBUS), J1.A9 (VBUS), J1.B4 (VBUS), J1.B9 (VBUS)
unnamed: J1.A5 (CC1), R5.1
unnamed: J1.B5 (CC2), R6.2
unnamed: R4.2, U1.14 (USB_D+/IO20)
unnamed: R3.1, U1.13 (USB_D-/IO19)
unnamed: R26.2, R27.2, U49.3 (D1)
RESET: C1.1, C3.2, R1.2, SW1.1 (A), U1.3 (EN)
RGB: U1.20 (IO12); also elsewhere on the board
RX: TP2.1, U1.36 (RXD0/IO44)
RotA1: U1.39 (IO1); also elsewhere on the board
RotA2: U1.31 (IO38); also elsewhere on the board
RotA3: U1.26 (IO45); also elsewhere on the board
RotB1: U1.15 (IO3); also elsewhere on the board
RotB2: U1.32 (MTCK/IO39); also elsewhere on the board
RotB3: U1.16 (IO46); also elsewhere on the board
S0: U1.22 (IO14); also elsewhere on the board
S1: U1.17 (IO9); also elsewhere on the board
S2: U1.18 (IO10); also elsewhere on the board
S3: U1.19 (IO11); also elsewhere on the board
Switch1: U1.24 (IO47); also elsewhere on the board
Switch2: U1.25 (IO48); also elsewhere on the board
Switch3: R2.1, U1.27 (IO0); also elsewhere on the board
TMC1_DIR: U1.21 (IO13); also elsewhere on the board
TMC1_PD_UART: U1.4 (IO4); also elsewhere on the board
TMC1_STEP: U1.38 (IO2); also elsewhere on the board
TMC2_DIR: U1.8 (IO15); also elsewhere on the board
TMC2_PD_UART: U1.9 (IO16); also elsewhere on the board
TMC2_STEP: U1.5 (IO5); also elsewhere on the board
TMC3_DIR: U1.11 (IO18); also elsewhere on the board
TMC3_PD_UART: U1.23 (IO21); also elsewhere on the board
TMC3_STEP: U1.10 (IO17); also elsewhere on the board
TMC4_DIR: U1.34 (MTDI/IO41); also elsewhere on the board
TMC4_PD_UART: U1.35 (MTMS/IO42); also elsewhere on the board
TMC4_STEP: U1.33 (MTDO/IO40); also elsewhere on the board
TX: TP1.1, U1.37 (TXD0/IO43)

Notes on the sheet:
5v to 3v3 LDO
LRS-350-24 Power Supply
ESP32-S3 MCU
Reset Button
Autoswitching power mux
USB-C PD
module here
UART Debugging
External 24V -> 5v DC-DC Buck Converter Module

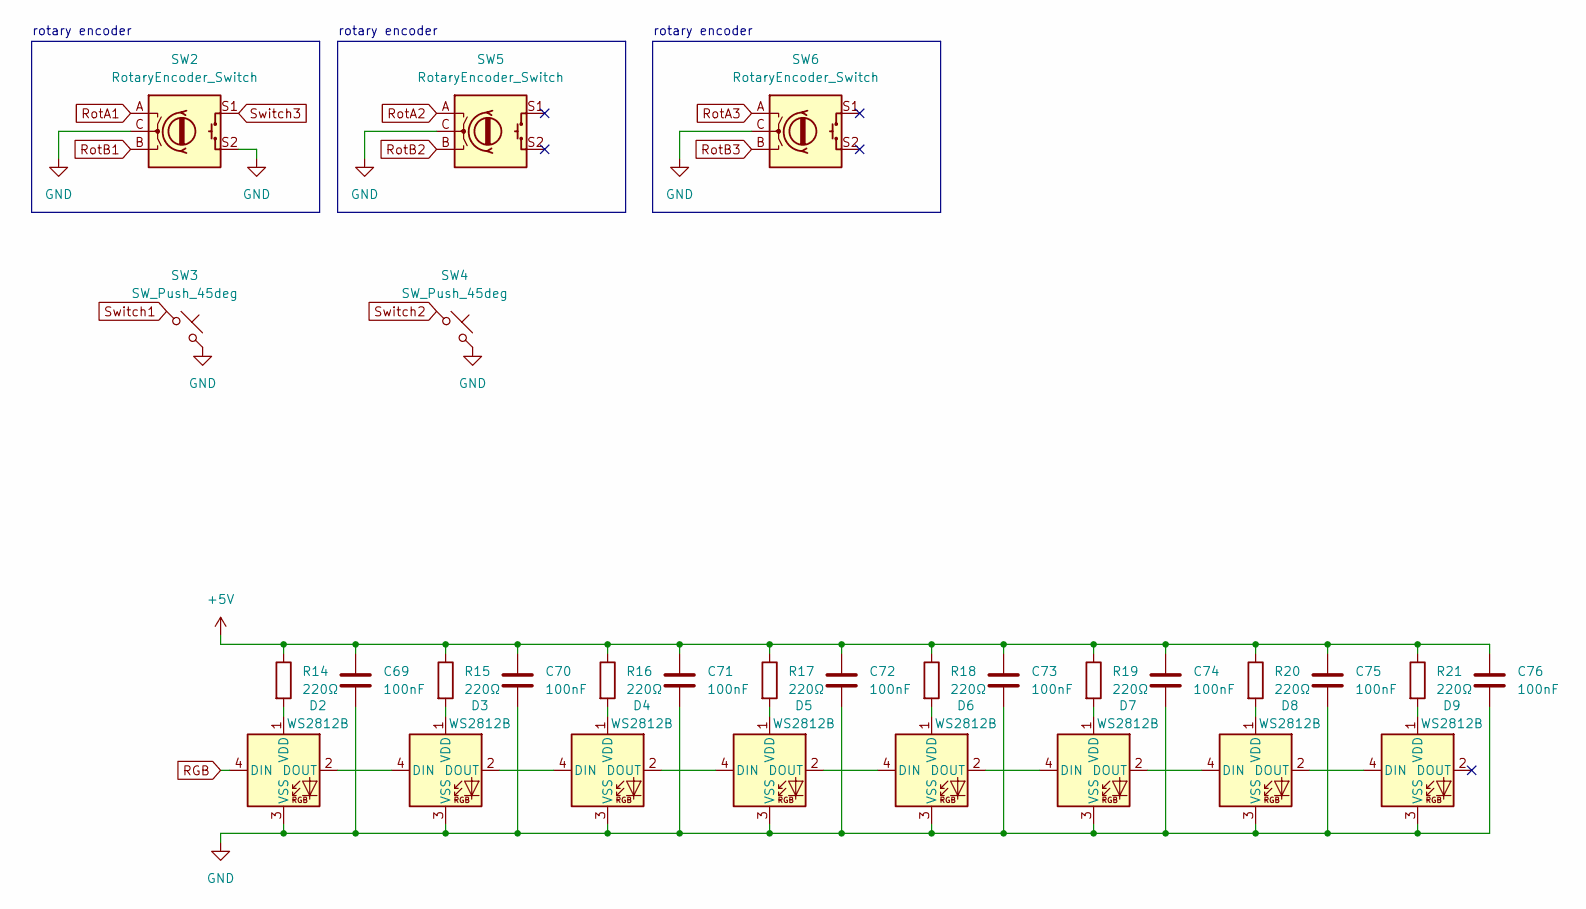
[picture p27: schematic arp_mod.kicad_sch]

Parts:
C69, C70, C71, C72, C73, C74, C75, C76: 100nF; C_0805_2012Metric
D2, D3, D4, D5, D6, D7, D8, D9: WS2812B; LED_WS2812B_PLCC4_5.0x5.0mm_P3.2mm
R14, R15, R16, R17, R18, R19, R20, R21: 220Ω; R_0805_2012Metric
SW2, SW5, SW6: RotaryEncoder_Switch; RotaryEncoder_Alps_EC11E-Switch_Vertical_H20mm
SW3, SW4: SW_Push_45deg; TH_L10.9-W5.9-CPG151101S11

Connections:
+5V: C69.1, C70.1, C71.1, C72.1, C73.1, C74.1, C75.1, C76.1, R14.1, R15.1, R16.1, R17.1, R18.1, R19.1, R20.1, R21.1; also elsewhere on the board
GND: C69.2, C70.2, C71.2, C72.2, C73.2, C74.2, C75.2, C76.2, D2.3 (VSS), D3.3 (VSS), D4.3 (VSS), D5.3 (VSS), D6.3 (VSS), D7.3 (VSS), D8.3 (VSS), D9.3 (VSS), SW2.C, SW2.S2, SW3.2, SW4.2, SW5.C, SW6.C; also elsewhere on the board
unnamed: D2.2 (DOUT), D3.4 (DIN)
unnamed: D2.1 (VDD), R14.2
unnamed: D3.2 (DOUT), D4.4 (DIN)
unnamed: D3.1 (VDD), R15.2
unnamed: D4.2 (DOUT), D5.4 (DIN)
unnamed: D4.1 (VDD), R16.2
unnamed: D5.2 (DOUT), D6.4 (DIN)
unnamed: D5.1 (VDD), R17.2
unnamed: D6.2 (DOUT), D7.4 (DIN)
unnamed: D6.1 (VDD), R18.2
unnamed: D7.2 (DOUT), D8.4 (DIN)
unnamed: D7.1 (VDD), R19.2
unnamed: D8.2 (DOUT), D9.4 (DIN)
unnamed: D8.1 (VDD), R20.2
unnamed: D9.1 (VDD), R21.2
RGB: D2.4 (DIN); also elsewhere on the board
RotA1: SW2.A; also elsewhere on the board
RotA2: SW5.A; also elsewhere on the board
RotA3: SW6.A; also elsewhere on the board
RotB1: SW2.B; also elsewhere on the board
RotB2: SW5.B; also elsewhere on the board
RotB3: SW6.B; also elsewhere on the board
Switch1: SW3.1; also elsewhere on the board
Switch2: SW4.1; also elsewhere on the board
Switch3: SW2.S1; also elsewhere on the board

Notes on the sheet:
rotary encoder

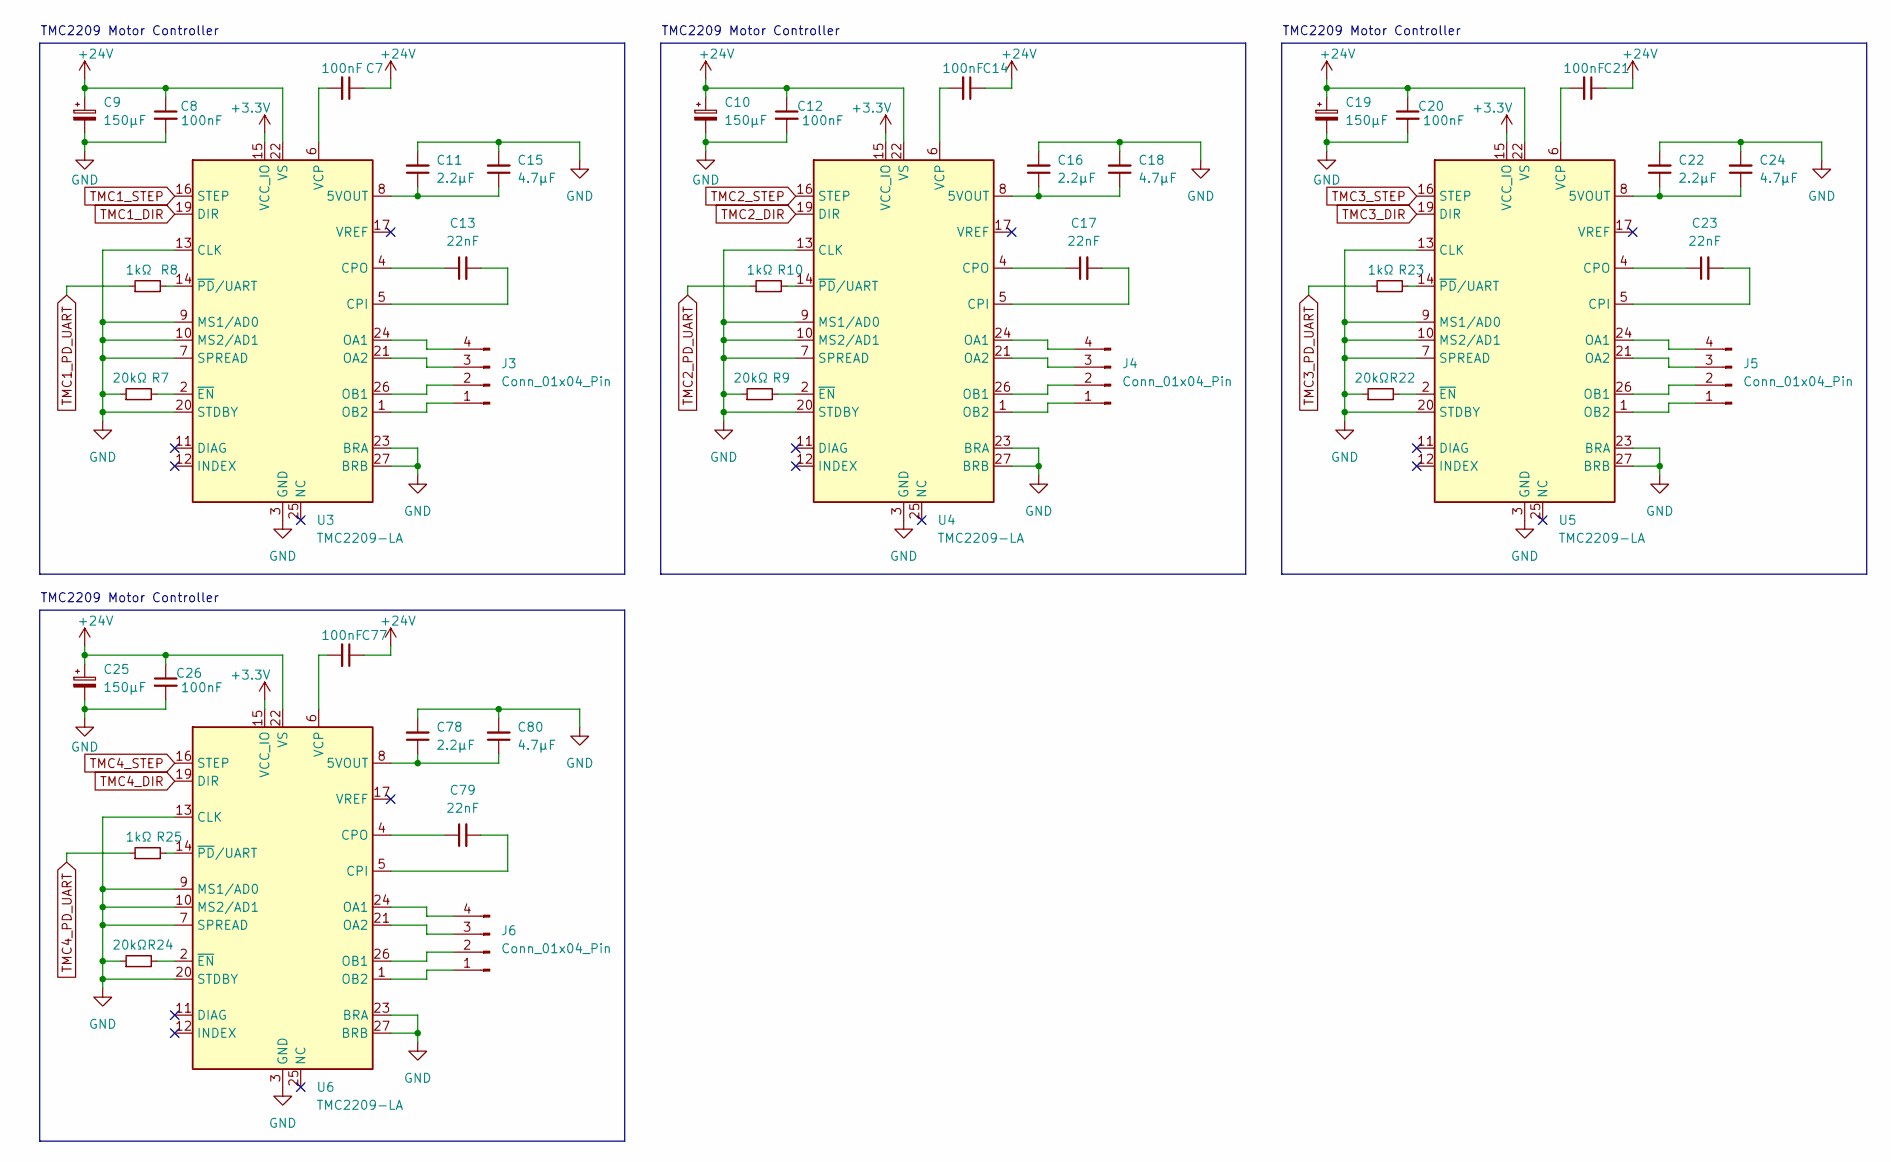
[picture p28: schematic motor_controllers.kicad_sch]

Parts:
C7, C8, C12, C14, C20, C21, C26, C77: 100nF; C_0805_2012Metric
C9, C10, C19, C25: 150µF; C_Radial_D10.0mm_H12.5mm_P5.00mm
C11, C16, C22, C78: 2.2µF; C_0805_2012Metric
C13, C17, C23, C79: 22nF; C_0805_2012Metric
C15, C18, C24, C80: 4.7µF; C_0805_2012Metric
J3, J4, J5, J6: Conn_01x04_Pin; PinHeader_1x04_P2.54mm_Vertical
R7, R9, R22, R24: 20kΩ; R_0805_2012Metric
R8, R10, R23, R25: 1kΩ; R_0805_2012Metric
U3, U4, U5, U6: TMC2209-LA; VQFN-28-1EP_5x5mm_P0.5mm_EP3.7x3.7mm_ThermalVias

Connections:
+3.3V: U3.15 (VCC_IO), U4.15 (VCC_IO), U5.15 (VCC_IO), U6.15 (VCC_IO); also elsewhere on the board
+24V: C7.1, C8.1, C9.1, C10.1, C12.1, C14.1, C19.1, C20.1, C21.1, C25.1, C26.1, C77.1, U3.22 (VS), U3.28 (VS), U4.22 (VS), U4.28 (VS), U5.22 (VS), U5.28 (VS), U6.22 (VS), U6.28 (VS); also elsewhere on the board
GND: C8.2, C9.2, C10.2, C11.2, C12.2, C15.2, C16.2, C18.2, C19.2, C20.2, C22.2, C24.2, C25.2, C26.2, C78.2, C80.2, R7.1, R9.1, R22.1, R24.1, U3.3 (GND), U3.7 (SPREAD), U3.9 (MS1/AD0), U3.10 (MS2/AD1), U3.13 (CLK), U3.18 (GND), U3.20 (STDBY), U3.23 (BRA), U3.27 (BRB), U3.29 (GND), U4.3 (GND), U4.7 (SPREAD), U4.9 (MS1/AD0), U4.10 (MS2/AD1), U4.13 (CLK), U4.18 (GND), U4.20 (STDBY), U4.23 (BRA), U4.27 (BRB), U4.29 (GND), U5.3 (GND), U5.7 (SPREAD), U5.9 (MS1/AD0), U5.10 (MS2/AD1), U5.13 (CLK), U5.18 (GND), U5.20 (STDBY), U5.23 (BRA), U5.27 (BRB), U5.29 (GND), U6.3 (GND), U6.7 (SPREAD), U6.9 (MS1/AD0), U6.10 (MS2/AD1), U6.13 (CLK), U6.18 (GND), U6.20 (STDBY), U6.23 (BRA), U6.27 (BRB), U6.29 (GND); also elsewhere on the board
unnamed: J3.1, U3.1 (OB2)
unnamed: J3.2, U3.26 (OB1)
unnamed: J3.3, U3.21 (OA2)
unnamed: J3.4, U3.24 (OA1)
unnamed: J4.1, U4.1 (OB2)
unnamed: J4.2, U4.26 (OB1)
unnamed: J4.3, U4.21 (OA2)
unnamed: J4.4, U4.24 (OA1)
unnamed: J5.1, U5.1 (OB2)
unnamed: J5.2, U5.26 (OB1)
unnamed: J5.3, U5.21 (OA2)
unnamed: J5.4, U5.24 (OA1)
unnamed: J6.1, U6.1 (OB2)
unnamed: J6.2, U6.26 (OB1)
unnamed: J6.3, U6.21 (OA2)
unnamed: J6.4, U6.24 (OA1)
unnamed: C11.1, C15.1, U3.8 (5VOUT)
unnamed: C13.2, U3.5 (CPI)
unnamed: C13.1, U3.4 (CPO)
unnamed: C7.2, U3.6 (VCP)
unnamed: R7.2, U3.2 (~EN)
unnamed: R8.2, U3.14 (~PD/UART)
unnamed: C16.1, C18.1, U4.8 (5VOUT)
unnamed: C17.2, U4.5 (CPI)
unnamed: C17.1, U4.4 (CPO)
unnamed: C14.2, U4.6 (VCP)
unnamed: R9.2, U4.2 (~EN)
unnamed: R10.2, U4.14 (~PD/UART)
unnamed: C22.1, C24.1, U5.8 (5VOUT)
unnamed: C23.2, U5.5 (CPI)
unnamed: C23.1, U5.4 (CPO)
unnamed: C21.2, U5.6 (VCP)
unnamed: R22.2, U5.2 (~EN)
unnamed: R23.2, U5.14 (~PD/UART)
unnamed: C78.1, C80.1, U6.8 (5VOUT)
unnamed: C79.2, U6.5 (CPI)
unnamed: C79.1, U6.4 (CPO)
unnamed: C77.2, U6.6 (VCP)
unnamed: R24.2, U6.2 (~EN)
unnamed: R25.2, U6.14 (~PD/UART)
TMC1_DIR: U3.19 (DIR); also elsewhere on the board
TMC1_PD_UART: R8.1; also elsewhere on the board
TMC1_STEP: U3.16 (STEP); also elsewhere on the board
TMC2_DIR: U4.19 (DIR); also elsewhere on the board
TMC2_PD_UART: R10.1; also elsewhere on the board
TMC2_STEP: U4.16 (STEP); also elsewhere on the board
TMC3_DIR: U5.19 (DIR); also elsewhere on the board
TMC3_PD_UART: R23.1; also elsewhere on the board
TMC3_STEP: U5.16 (STEP); also elsewhere on the board
TMC4_DIR: U6.19 (DIR); also elsewhere on the board
TMC4_PD_UART: R25.1; also elsewhere on the board
TMC4_STEP: U6.16 (STEP); also elsewhere on the board

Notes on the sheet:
TMC2209 Motor Controller

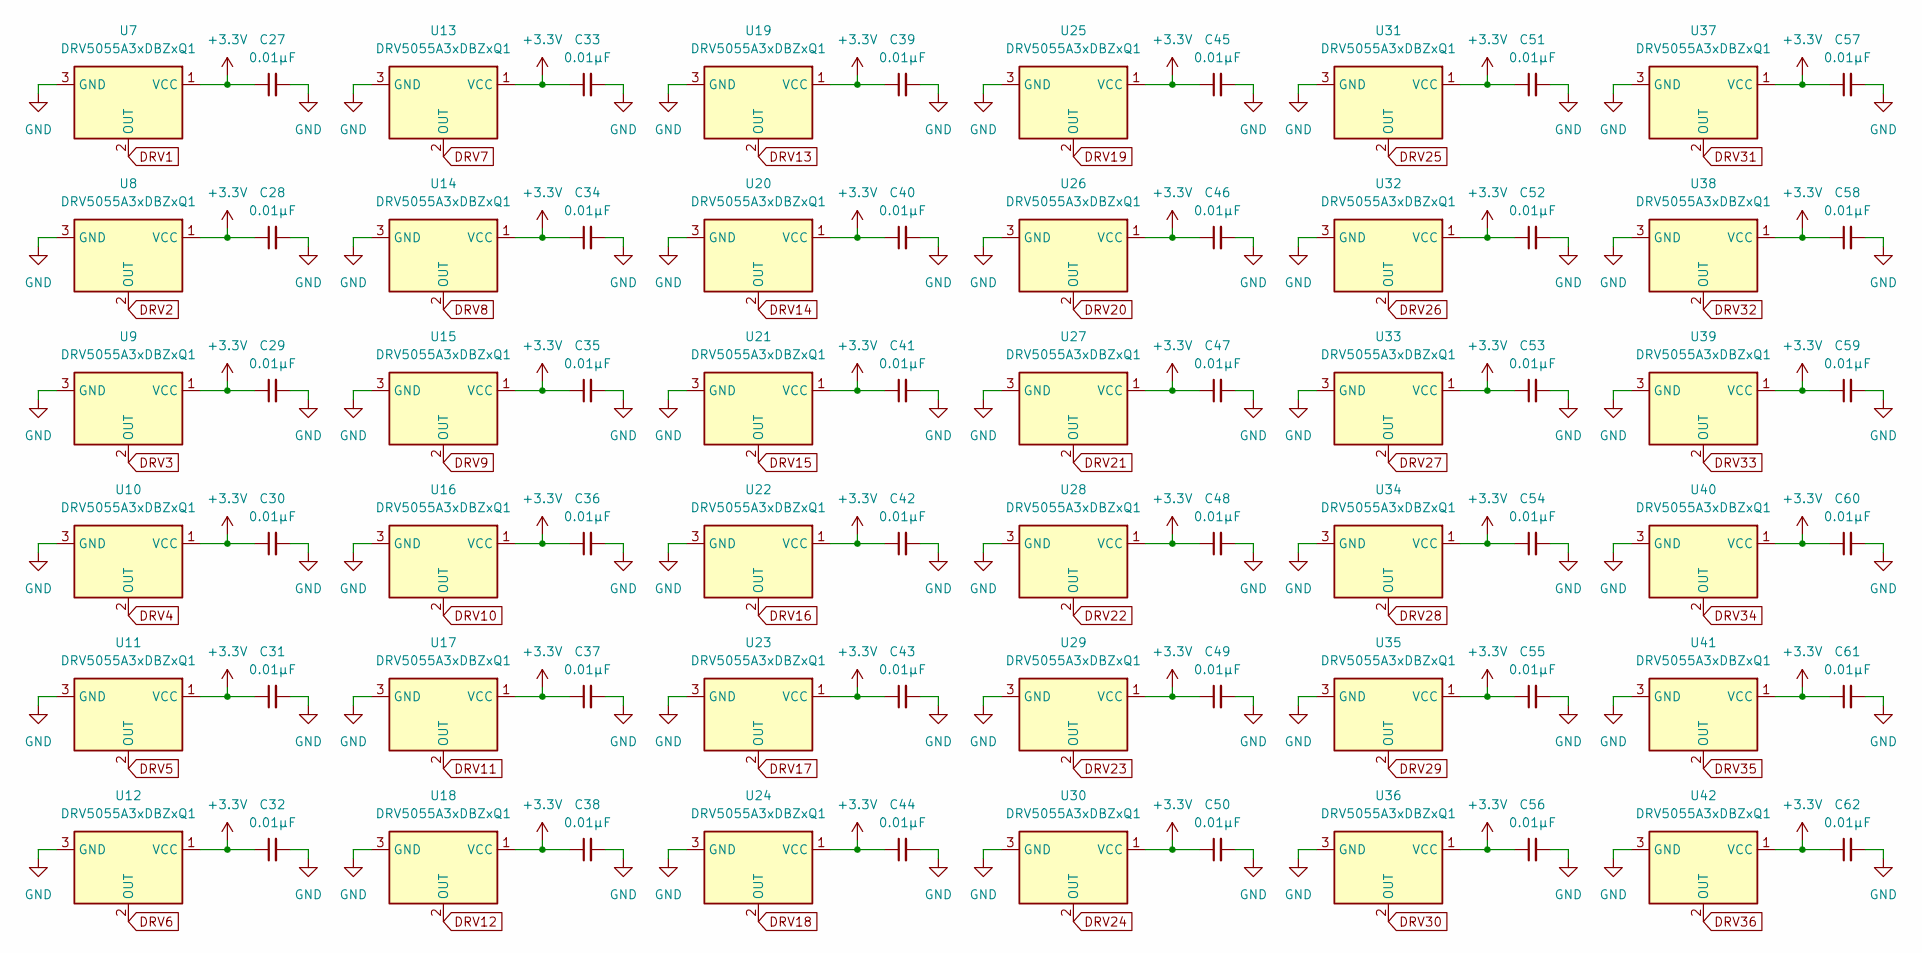
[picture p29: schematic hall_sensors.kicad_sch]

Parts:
C27, C28, C29, C30, C31, C32, C33, C34, C35, C36, C37, C38, C39, C40, C41, C42, C43, C44, C45, C46, C47, C48, C49, C50, C51, C52, C53, C54, C55, C56, C57, C58, C59, C60, C61, C62: 0.01µF; C_0805_2012Metric
U7, U8, U9, U10, U11, U12, U13, U14, U15, U16, U17, U18, U19, U20, U21, U22, U23, U24, U25, U26, U27, U28, U29, U30, U31, U32, U33, U34, U35, U36, U37, U38, U39, U40, U41, U42: DRV5055A3xDBZxQ1; SOT-23

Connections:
+3.3V: C27.1, C28.1, C29.1, C30.1, C31.1, C32.1, C33.1, C34.1, C35.1, C36.1, C37.1, C38.1, C39.1, C40.1, C41.1, C42.1, C43.1, C44.1, C45.1, C46.1, C47.1, C48.1, C49.1, C50.1, C51.1, C52.1, C53.1, C54.1, C55.1, C56.1, C57.1, C58.1, C59.1, C60.1, C61.1, C62.1, U7.1 (VCC), U8.1 (VCC), U9.1 (VCC), U10.1 (VCC), U11.1 (VCC), U12.1 (VCC), U13.1 (VCC), U14.1 (VCC), U15.1 (VCC), U16.1 (VCC), U17.1 (VCC), U18.1 (VCC), U19.1 (VCC), U20.1 (VCC), U21.1 (VCC), U22.1 (VCC), U23.1 (VCC), U24.1 (VCC), U25.1 (VCC), U26.1 (VCC), U27.1 (VCC), U28.1 (VCC), U29.1 (VCC), U30.1 (VCC), U31.1 (VCC), U32.1 (VCC), U33.1 (VCC), U34.1 (VCC), U35.1 (VCC), U36.1 (VCC), U37.1 (VCC), U38.1 (VCC), U39.1 (VCC), U40.1 (VCC), U41.1 (VCC), U42.1 (VCC); also elsewhere on the board
DRV1: U7.2 (OUT); also elsewhere on the board
DRV2: U8.2 (OUT); also elsewhere on the board
DRV3: U9.2 (OUT); also elsewhere on the board
DRV4: U10.2 (OUT); also elsewhere on the board
DRV5: U11.2 (OUT); also elsewhere on the board
DRV6: U12.2 (OUT); also elsewhere on the board
DRV7: U13.2 (OUT); also elsewhere on the board
DRV8: U14.2 (OUT); also elsewhere on the board
DRV9: U15.2 (OUT); also elsewhere on the board
DRV10: U16.2 (OUT); also elsewhere on the board
DRV11: U17.2 (OUT); also elsewhere on the board
DRV12: U18.2 (OUT); also elsewhere on the board
DRV13: U19.2 (OUT); also elsewhere on the board
DRV14: U20.2 (OUT); also elsewhere on the board
DRV15: U21.2 (OUT); also elsewhere on the board
DRV16: U22.2 (OUT); also elsewhere on the board
DRV17: U23.2 (OUT); also elsewhere on the board
DRV18: U24.2 (OUT); also elsewhere on the board
DRV19: U25.2 (OUT); also elsewhere on the board
DRV20: U26.2 (OUT); also elsewhere on the board
DRV21: U27.2 (OUT); also elsewhere on the board
DRV22: U28.2 (OUT); also elsewhere on the board
DRV23: U29.2 (OUT); also elsewhere on the board
DRV24: U30.2 (OUT); also elsewhere on the board
DRV25: U31.2 (OUT); also elsewhere on the board
DRV26: U32.2 (OUT); also elsewhere on the board
DRV27: U33.2 (OUT); also elsewhere on the board
DRV28: U34.2 (OUT); also elsewhere on the board
DRV29: U35.2 (OUT); also elsewhere on the board
DRV30: U36.2 (OUT); also elsewhere on the board
DRV31: U37.2 (OUT); also elsewhere on the board
DRV32: U38.2 (OUT); also elsewhere on the board
DRV33: U39.2 (OUT); also elsewhere on the board
DRV34: U40.2 (OUT); also elsewhere on the board
DRV35: U41.2 (OUT); also elsewhere on the board
DRV36: U42.2 (OUT); also elsewhere on the board
GND: C27.2, C28.2, C29.2, C30.2, C31.2, C32.2, C33.2, C34.2, C35.2, C36.2, C37.2, C38.2, C39.2, C40.2, C41.2, C42.2, C43.2, C44.2, C45.2, C46.2, C47.2, C48.2, C49.2, C50.2, C51.2, C52.2, C53.2, C54.2, C55.2, C56.2, C57.2, C58.2, C59.2, C60.2, C61.2, C62.2, U7.3 (GND), U8.3 (GND), U9.3 (GND), U10.3 (GND), U11.3 (GND), U12.3 (GND), U13.3 (GND), U14.3 (GND), U15.3 (GND), U16.3 (GND), U17.3 (GND), U18.3 (GND), U19.3 (GND), U20.3 (GND), U21.3 (GND), U22.3 (GND), U23.3 (GND), U24.3 (GND), U25.3 (GND), U26.3 (GND), U27.3 (GND), U28.3 (GND), U29.3 (GND), U30.3 (GND), U31.3 (GND), U32.3 (GND), U33.3 (GND), U34.3 (GND), U35.3 (GND), U36.3 (GND), U37.3 (GND), U38.3 (GND), U39.3 (GND), U40.3 (GND), U41.3 (GND), U42.3 (GND); also elsewhere on the board

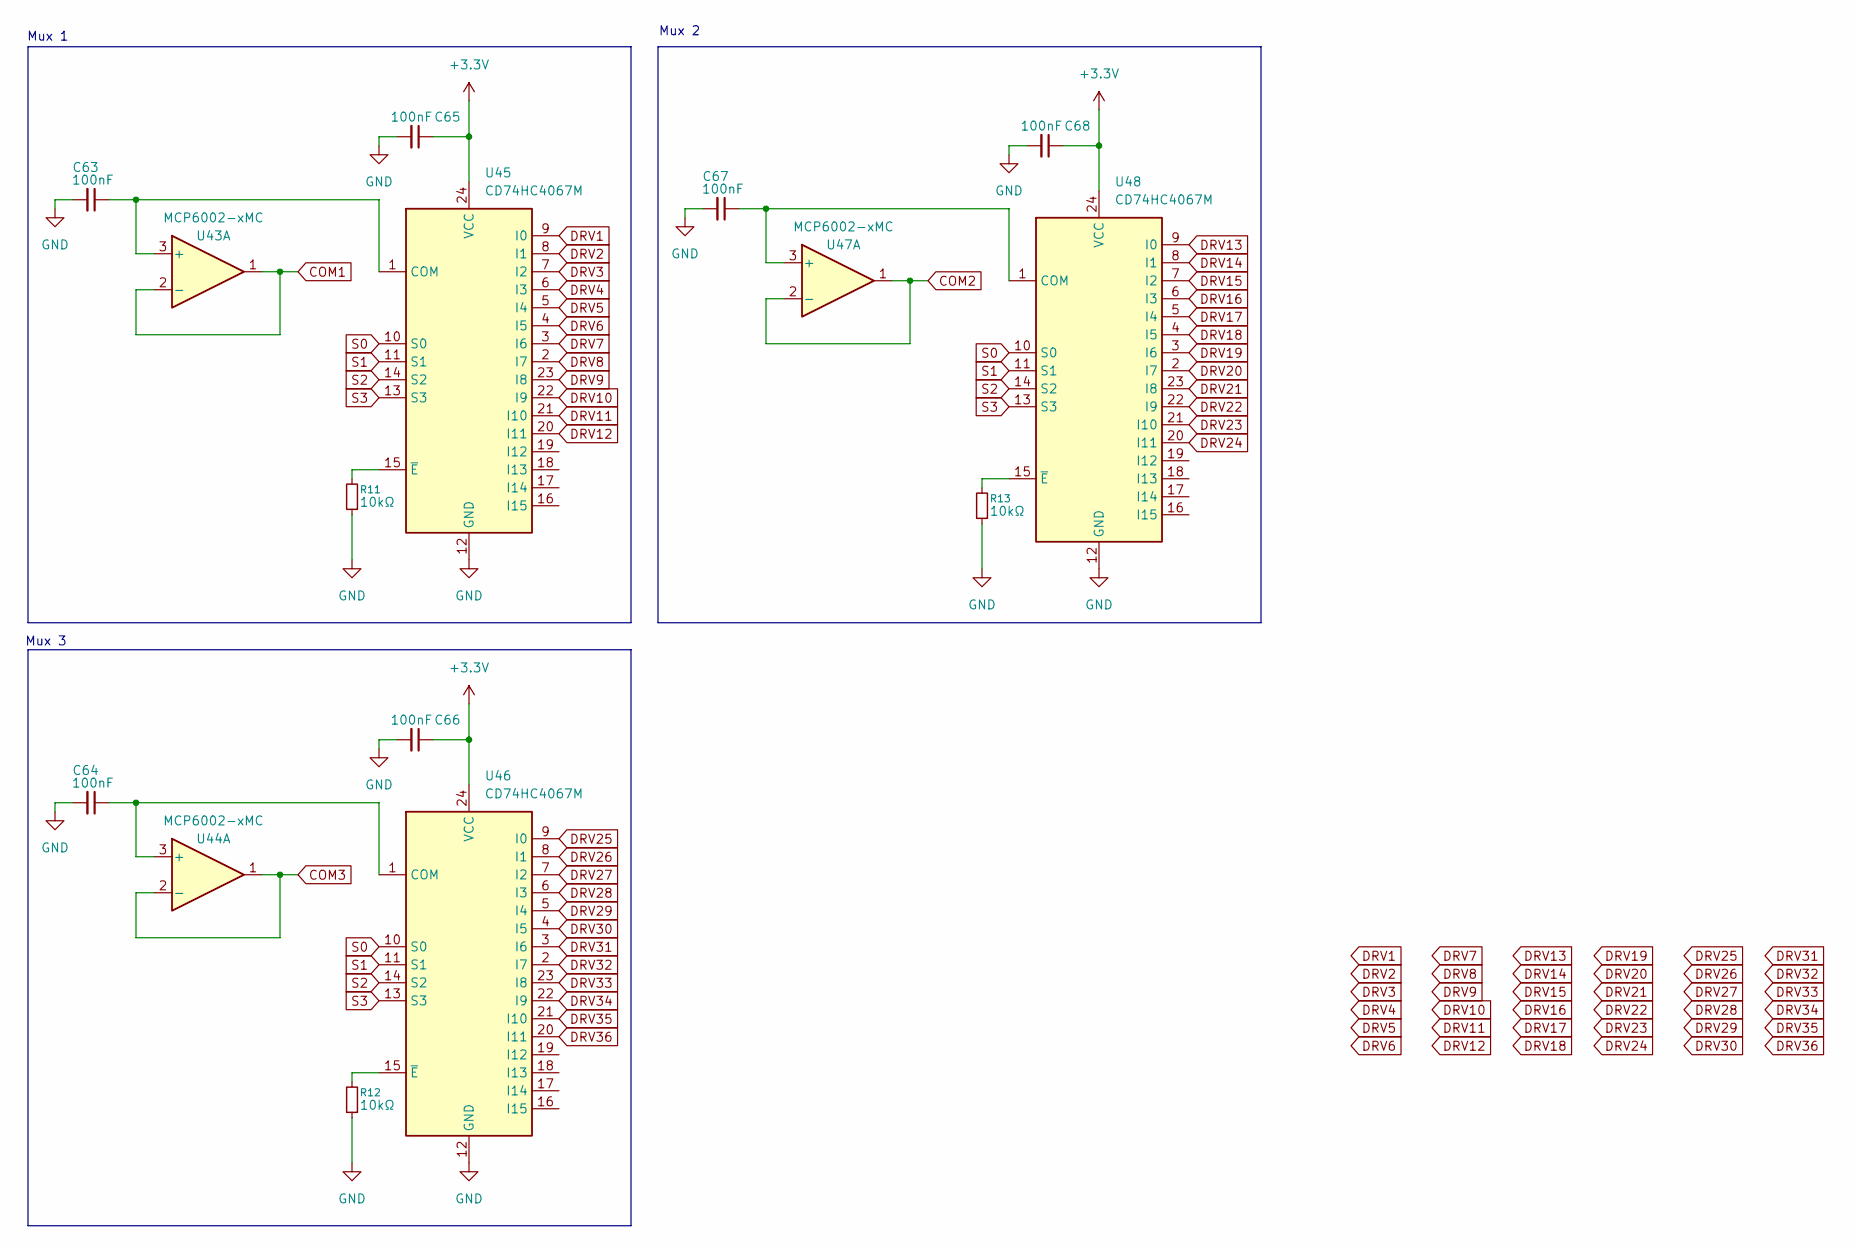
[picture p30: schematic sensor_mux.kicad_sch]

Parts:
C63, C64, C65, C66, C67, C68: 100nF; C_0805_2012Metric
R11, R12, R13: 10kΩ; R_0805_2012Metric
U43, U44, U47: MCP6002-xMC; DFN-8-1EP_3x2mm_P0.5mm_EP1.75x1.45mm
U45, U46, U48: CD74HC4067M; SOIC-24W_7.5x15.4mm_P1.27mm

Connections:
+3.3V: C65.1, C66.1, C68.1, U45.24 (VCC), U46.24 (VCC), U48.24 (VCC); also elsewhere on the board
COM1: U43.1, U43.2 (-); also elsewhere on the board
COM2: U47.1, U47.2 (-); also elsewhere on the board
COM3: U44.1, U44.2 (-); also elsewhere on the board
DRV1: U45.9 (I0); also elsewhere on the board
DRV2: U45.8 (I1); also elsewhere on the board
DRV3: U45.7 (I2); also elsewhere on the board
DRV4: U45.6 (I3); also elsewhere on the board
DRV5: U45.5 (I4); also elsewhere on the board
DRV6: U45.4 (I5); also elsewhere on the board
DRV7: U45.3 (I6); also elsewhere on the board
DRV8: U45.2 (I7); also elsewhere on the board
DRV9: U45.23 (I8); also elsewhere on the board
DRV10: U45.22 (I9); also elsewhere on the board
DRV11: U45.21 (I10); also elsewhere on the board
DRV12: U45.20 (I11); also elsewhere on the board
DRV13: U48.9 (I0); also elsewhere on the board
DRV14: U48.8 (I1); also elsewhere on the board
DRV15: U48.7 (I2); also elsewhere on the board
DRV16: U48.6 (I3); also elsewhere on the board
DRV17: U48.5 (I4); also elsewhere on the board
DRV18: U48.4 (I5); also elsewhere on the board
DRV19: U48.3 (I6); also elsewhere on the board
DRV20: U48.2 (I7); also elsewhere on the board
DRV21: U48.23 (I8); also elsewhere on the board
DRV22: U48.22 (I9); also elsewhere on the board
DRV23: U48.21 (I10); also elsewhere on the board
DRV24: U48.20 (I11); also elsewhere on the board
DRV25: U46.9 (I0); also elsewhere on the board
DRV26: U46.8 (I1); also elsewhere on the board
DRV27: U46.7 (I2); also elsewhere on the board
DRV28: U46.6 (I3); also elsewhere on the board
DRV29: U46.5 (I4); also elsewhere on the board
DRV30: U46.4 (I5); also elsewhere on the board
DRV31: U46.3 (I6); also elsewhere on the board
DRV32: U46.2 (I7); also elsewhere on the board
DRV33: U46.23 (I8); also elsewhere on the board
DRV34: U46.22 (I9); also elsewhere on the board
DRV35: U46.21 (I10); also elsewhere on the board
DRV36: U46.20 (I11); also elsewhere on the board
GND: C63.2, C64.2, C65.2, C66.2, C67.2, C68.2, R11.1, R12.1, R13.1, U45.12 (GND), U46.12 (GND), U48.12 (GND); also elsewhere on the board
unnamed: C63.1, U43.3 (+), U45.1 (COM)
unnamed: C64.1, U44.3 (+), U46.1 (COM)
unnamed: R11.2, U45.15 (~E)
unnamed: R12.2, U46.15 (~E)
unnamed: C67.1, U47.3 (+), U48.1 (COM)
unnamed: R13.2, U48.15 (~E)
S0: U45.10 (S0), U46.10 (S0), U48.10 (S0); also elsewhere on the board
S1: U45.11 (S1), U46.11 (S1), U48.11 (S1); also elsewhere on the board
S2: U45.14 (S2), U46.14 (S2), U48.14 (S2); also elsewhere on the board
S3: U45.13 (S3), U46.13 (S3), U48.13 (S3); also elsewhere on the board

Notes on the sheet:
Mux 3
Mux 1
Mux 2

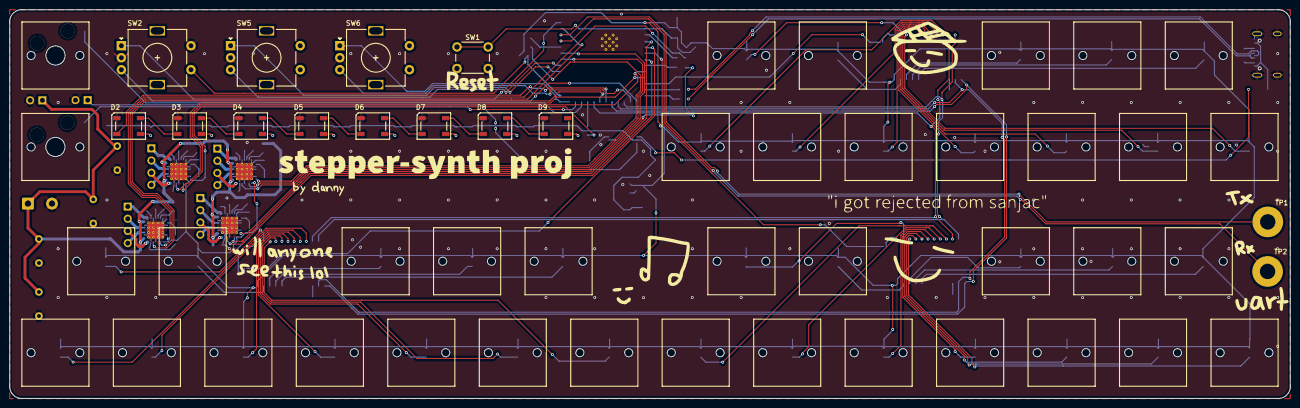
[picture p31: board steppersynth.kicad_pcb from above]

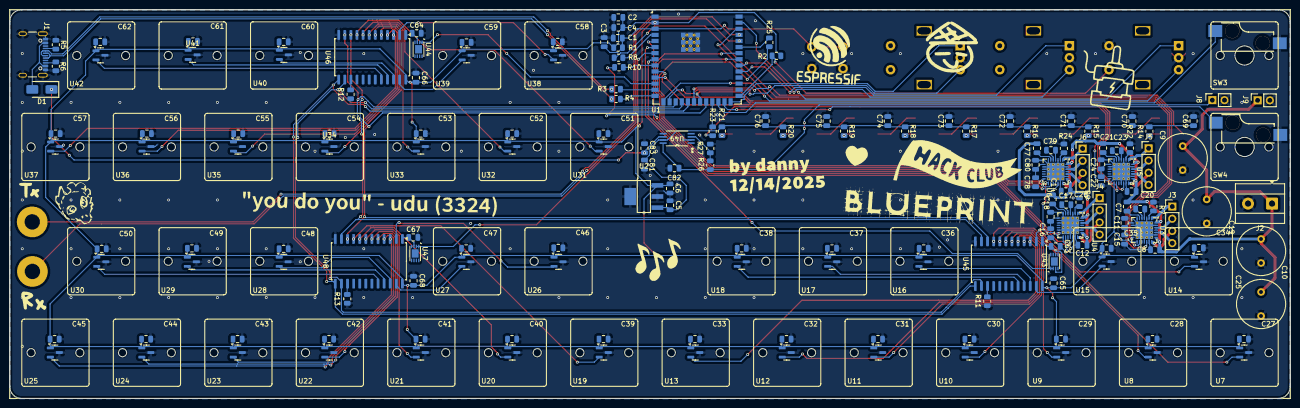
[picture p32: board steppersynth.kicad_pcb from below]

Board: 2 copper layers, 266.7 x 81.0 mm, 184 parts (170 on the bottom side), 143 nets.

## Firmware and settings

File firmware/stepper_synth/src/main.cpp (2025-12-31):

#include <Arduino.h>

#include <TMCStepper.h>
#include <CD74HC4067.h>
#include <FastLED.h>
#include <ESP32Encoder.h>

// --------------------- analog mux 2 hall sensors ---------------------

CD74HC4067 mux(14, 9, 10, 11); //mux control pins shared between 3 muxes

const int g_common_pin_1 = 6; //mux 1 out
const int g_common_pin_2 = 7; //mux 2 out
const int g_common_pin_3 = 8; //mux 3 out



// --------------------- neopixels ---------------------

#define NUM_LEDS  8
#define DATA_PIN 12
CRGB leds[NUM_LEDS];



// --------------------- buttons ---------------------

#define BTN_1 47
#define BTN_2 48
#define BTN_3  0 //rotary


// --------------------- rotary encoders ---------------------

#define ROTARY_A1  1
#define ROTARY_B1  3
#define ROTARY_A2 38
#define ROTARY_B2 39
#define ROTARY_A3 45
#define ROTARY_B3 46

ESP32Encoder encoder1;
ESP32Encoder encoder2;
ESP32Encoder encoder3;



// --------------------- tmc2209 nema 17 motors ---------------------

// ty <3 https://forum.arduino.cc/t/tmcstepper-arduino-tmc2209/956036

#define STEP_PIN_1     2
#define DIR_PIN_1     13
#define PD_UART_PIN_1  4

#define STEP_PIN_2     5
#define DIR_PIN_2     15
#define PD_UART_PIN_2 16

#define STEP_PIN_3    17
#define DIR_PIN_3     18
#define PD_UART_PIN_3 21

#define STEP_PIN_4    40
#define DIR_PIN_4     41
#define PD_UART_PIN_4 42

#define R_SENSE 0.11f
#define DRIVER_1_ADDRESS 0b00
#define DRIVER_2_ADDRESS 0b01
#define DRIVER_3_ADDRESS 0b10
#define DRIVER_4_ADDRESS 0b11

HardwareSerial serial_1(1);
HardwareSerial serial_2(2);
HardwareSerial serial_3(0);
HardwareSerial serial_4(1);

TMC2209Stepper driver_1(&serial_1, R_SENSE, DRIVER_1_ADDRESS);
TMC2209Stepper driver_2(&serial_2, R_SENSE, DRIVER_2_ADDRESS);
TMC2209Stepper driver_3(&serial_3, R_SENSE, DRIVER_3_ADDRESS);
TMC2209Stepper driver_4(&serial_4, R_SENSE, DRIVER_4_ADDRESS);

void setupDriver(TMC2209Stepper &driver) {
  driver.begin();
  driver.toff(5);
  driver.blank_time(24);

  driver.rms_current(800);
  driver.microsteps(16);
  driver.en_spreadCycle(false);
  driver.pwm_autoscale(true);

  driver.TCOOLTHRS(0xFFFFF);
  driver.SGTHRS(0xFF);
}

void setup() {

  Serial.begin(115200);

  // CD74HC4067 mux setup
  
  pinMode(g_common_pin_1, OUTPUT);
  pinMode(g_common_pin_2, OUTPUT);
  pinMode(g_common_pin_3, OUTPUT);

  // ws2812 neopixel setup

  FastLED.addLeds<NEOPIXEL, DATA_PIN>(leds, NUM_LEDS);

  // button setup

  pinMode(BTN_1, INPUT_PULLUP);
  pinMode(BTN_2, INPUT_PULLUP);
  pinMode(BTN_3, INPUT_PULLUP);

  // encoder setup

  encoder1.attachSingleEdge(ROTARY_A1, ROTARY_B1);
  encoder1.setCount(0);

  encoder2.attachSingleEdge(ROTARY_A2, ROTARY_B2);
  encoder2.setCount(0);

  encoder3.attachSingleEdge(ROTARY_A3, ROTARY_B3);
  encoder3.setCount(0);

  // tmc2209 driver setup

  serial_1.begin(115200, SERIAL_8N1, -1, PD_UART_PIN_1);
  serial_2.begin(115200, SERIAL_8N1, -1, PD_UART_PIN_2);
  serial_3.begin(115200, SERIAL_8N1, -1, PD_UART_PIN_3);
  serial_4.begin(115200, SERIAL_8N1, -1, PD_UART_PIN_4);

  setupDriver(driver_1);
  setupDriver(driver_2);
  setupDriver(driver_3);
  setupDriver(driver_4);

  pinMode(STEP_PIN_1, OUTPUT);
  pinMode(DIR_PIN_1, OUTPUT);
  pinMode(STEP_PIN_2, OUTPUT);
  pinMode(DIR_PIN_2, OUTPUT);
  pinMode(STEP_PIN_3, OUTPUT);
  pinMode(DIR_PIN_3, OUTPUT);
  pinMode(STEP_PIN_4, OUTPUT);
  pinMode(DIR_PIN_4, OUTPUT);
}

void loop() {
  leds[0] = CRGB::Red;
  FastLED.show();
  
  digitalWrite(STEP_PIN_1, HIGH);

  delayMicroseconds(500);

  leds[0] = CRGB::Black;
  FastLED.show();

  digitalWrite(STEP_PIN_1, LOW);

  delayMicroseconds(500);
}

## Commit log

2025-12-04 add kicad files + more
    [steppersynth.kicad_pcb, steppersynth.kicad_sch]
2025-12-07 update kicad stuff
    [arp_mod.kicad_sch, hall_sensors.kicad_sch, motor_controllers.kicad_sch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]
2025-12-07 fix tmc motor stuff + more
    [motor_controllers.kicad_sch]
2025-12-08 position everything in the pcb
    [motor_controllers.kicad_sch, steppersynth.kicad_pcb]
2025-12-09 dc-dc buck converter
    [cherry mx switch resized 2.step, cherry mx switch resized 2.stl, cherry mx switch.step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]
2025-12-13 fix some pcb layout stuff
    [steppersynth.kicad_pcb]
2025-12-14 finish tracing everything
    [motor_controllers.kicad_sch, steppersynth.kicad_pcb]
2025-12-15 add journal, readme, cad, and assets
    [BOM.csv, Simple-CherryMX-Keycap.stl, bom.csv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]
2025-12-15 add sample firmware
    [large_fat_32MB.csv]
2025-12-31 add libs and all pinout devices
